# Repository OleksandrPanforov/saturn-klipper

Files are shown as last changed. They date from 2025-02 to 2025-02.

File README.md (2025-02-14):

# Elegoo Saturn 1 with Klipper

## Table of contents

1. [What and why?](#1-what-and-why)
2. [Bill of materials](#2-bill-of-materials)
3. [Hardware setup](#3-hardware-setup)
4. [Software setup](#4-software-setup)
5. [Addons](#5-addons)
6. [Troubleshooting](#6-troubleshooting)
7. [My experience](#7-my-experience)
8. [Next steps](#8-next-steps)

## 1. What and why?

### What?
**Elegoo Saturn 1 resin printer with Klipper onboard.**
<p align="center">
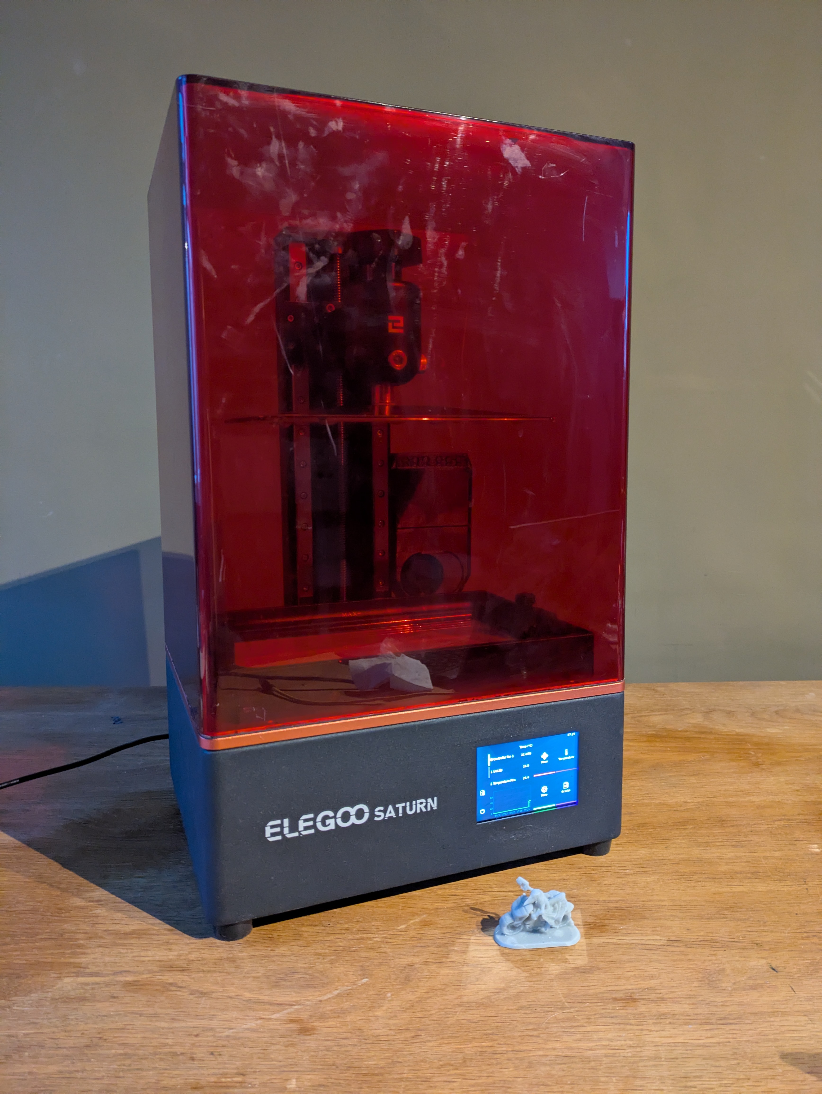
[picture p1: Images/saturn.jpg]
Saturn preview

</p>

Based on a donor printer, with or without a working screen, neatly packed in the stock enclosure. 
The older resin printers are dirt cheap and widely available, especially with a busted screen. That is, an easy and cost-effective starting point. 

### Why?
**I think, proprietary printers suck.** 

I've been working with resin printers for a while now, and the way any upgrade is either buying a new model, or perform complicated hacks is what I really disliked about the tech. Which is not the case with hobby-level FDM. 

Naturally, when I found out the [PR to get Klipper support for mSLA](https://github.com/Klipper3d/klipper/pull/6575) exists, I got an old Saturn and started tinkering. 

### Before you start
The Elegoo Saturn 1 was released in 2020 with a 8.9" 4k display onboard. By no means it is a modern printer with ultra-high resolution. That is, to set up the expectations, be aware this conversion might not suite your use case. Especially given the amount of tinkering required to make it work. As a cherry on top, just the electronics with a screen could easily cost the same as the new Elegoo Saturn 4. Not that I want to discourage you - this is an awesome project. Just be sure you understand what you are going to step into.

> ⚠️ And while we're on it, proceed at your own risk. I am not responsible for property damage, injuries, or any unwanted consequences occuring from following this manual. <br> <br>⚠️ It worked on my machine, that's the best I can tell. You have been warned.

## 2. Bill of materials

### Required
|Name|Qty|Note|
|-|-|-|
|[BTT Manta M4P](https://biqu.equipment/products/manta-m4p-m8p?variant=39847241056354)|1| |
|[Raspberry CM4](https://www.raspberrypi.com/products/compute-module-4/?variant=raspberry-pi-cm4001000)|1|**4Gb + Wifi + Lite recommended.** I was not able to use BTT CB1, due to troubles with configuring display with the proper overlay. |
|[CM4 cooling](https://www.waveshare.com/product/cm4-heatsink-b.htm) |1|Passive should work, active won't hurt for longer print jobs. |
|[TMC2209 stepper driver](https://biqu.equipment/products/bigtreetech-tmc2209-stepper-motor-driver-for-3d-printer-board-vs-tmc2208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) |1| |
|[PJ089Y2V5 8.9" mono screen](https://aliexpress.com/item/1005004398973695.html) |1|It is also possible to use TM089CFSP01 with the same config. |
|[HDMI driver for the display](https://aliexpress.com/item/1005004398973695.html) |1| |
|[BTT TFT35 SPI](https://biqu.equipment/products/bigtreetech-tft35-spi-v2-1-touchscreen-io2can-module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) |1|While not the best for the job, it fits best to the stock case. |
|HDMI cable |1|15-30cm, for connecting the HDMI driver |
|USB A to USB C cable |1|15-30cm, for connecting the HDMI driver. |
|KCD1 switch |1||
|5.5x2.5 power socket |1||
|[Printed parts]()|1||
|M3x40 screws|4||

### Reused from a donor printer
|Name|Qty|Note|
|-|-|-|
|NEMA17 stepper motor|1||
|Z axis kinematics|1||
|Z endstop|1|You will need to change the pinout of the connector.|
|Enclosure|1||
|Power supply unit|1||
|UV LED array with driver|1||
|Buildplate|1||
|Resin vat|1||
|Glass under the screen|1|Can be purchased with the screen, but reusing is slightly cheaper.|
|Enclosure fans|2||
|Most of the fasteners|1||

### Optional
|Name|Qty|Note|
|-|-|-|
|USB keystone |1||
|Temperature sensor|1| PT1000 is configured, it is a good option for monitoring the UV LED array temperature.|
|RJ45 keystone |1| |
|[SUNON 24V DC 0.65W 50x50x15mm](https://aliexpress.com/item/1005007898152811.html) |2|Stock fans can be reused.|
|[Nevermore Nano](https://www.printables.com/model/1176031-nevermore-v6-nano-single-fan-micro)|1|Any coal filter with fan will do. Strongly advised, resin fumes are a serious matter.|

## 3. Hardware setup
### Preparation
#### Screen
Important thing to consider when getting a Saturn is the screen model.
Originally, Saturns were shipped with either PJ089Y2V1 or TM089CFSP01.

> ❗ PJ089Y2V**5** has a different pinout from PJ089Y2V**1**, so HDMI driver will also be different.

#### Printed parts
ABS or ASA would be best to use. Little to no load expected on the printed parts, however there might be some relatively high temperatures around the UV LED array. 

#### Z-endstop
[EE-SX674](https://www.ia.omron.com/data_pdf/cat/ee-sx47_67_ds_e_13_4_csm483.pdf) with 3 pins connector should be wired as 

🟫Brown (5V)<br> 
🟦Blue (GND)<br>
⬛Black (Signal)

<p align="center">
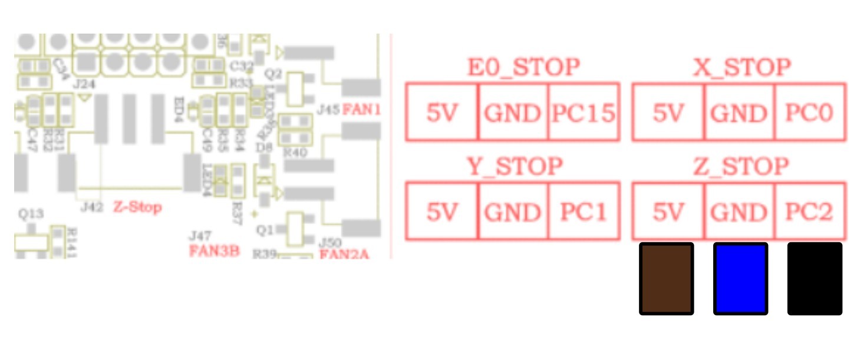
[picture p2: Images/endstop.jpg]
Z endstop wiring
    
</p>

### Disassembly 
From a donor printer, only enclosure, UV LED with driver and kinematics are needed. Screen only if it can be used with HDMI driver. 

### Assembly
0. Take the bottom part of the enclosure.
1. Install the BTT TFT35 using the printed mount. 
<p align="center">
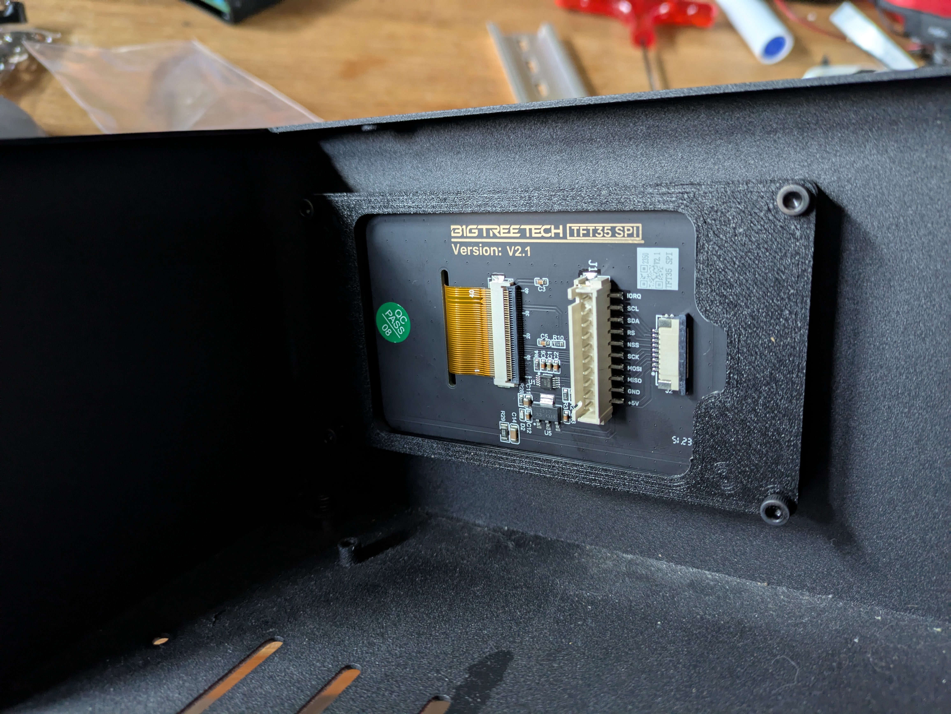
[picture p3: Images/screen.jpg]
BTT TFT35 mount
    
</p>

2. Insert the printed slot caps.
3. Install the mainboard using the printed mount.
4. Install the HDMI driver sing the printed mount.
5. Rotate and install the LED driver.

<p align="center">
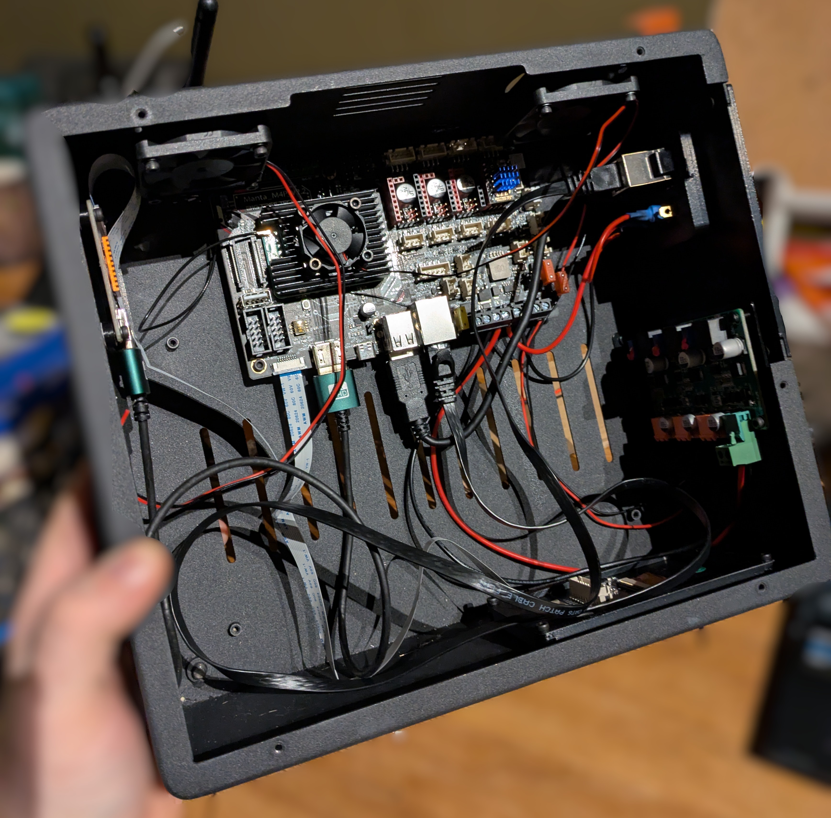
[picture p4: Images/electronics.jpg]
Electronics installed
    
</p>

6. Connect to the mainboard:
    + HDMI driver
    + LED driver
    + Power
    + BTT TFT35 SPI
    + Fans
    + Keystones, if used 

> ⚠️ This is the point where I suggest configuring the firmware, since after the UV LED is installed, the access to microsd card slot is tight, as well to the connectors.

7. Connect the UV LED array to the LED driver, then using the printed spacers and M3x40 screws install it in place.

<p align="center">
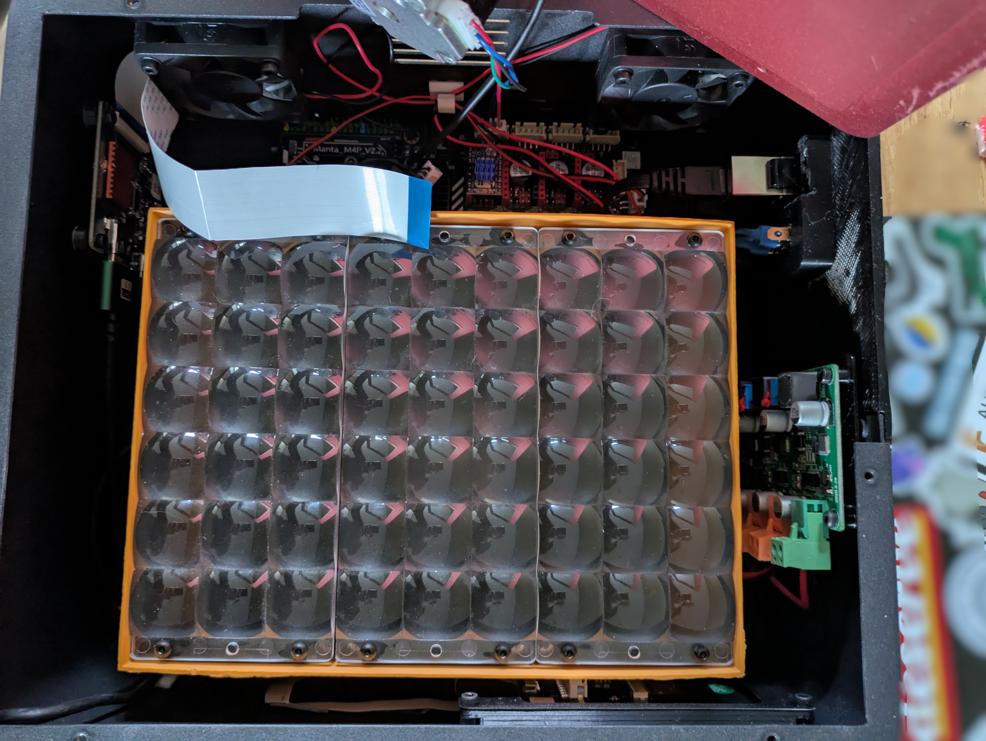
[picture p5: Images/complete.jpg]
UV LED array installed
    
</p>

> On this photo the stepper driver is in the wrong slot. It should be Z. Other than that, this is how everything should look at this point.
8. Connect to the mainboard:
    + Stepper motor
    + Z endstop
9. Connect the screen.
10. Screw the top part of the enclosure to the bottom. 
11. Calibrate as per [this guide](https://github.com/sn4k3/klipper-msla?tab=readme-ov-file#4-calibrate)
12. Make a test run as described in [this guide](https://github.com/sn4k3/klipper-msla?tab=readme-ov-file#5-final-run).

## 4. Software setup
### Firmware
Best starting point is [sn4k3/klipper-msla](https://github.com/sn4k3/klipper-msla). 
When following the manual, keep in mind the MCU is different, refer to [printer.cfg](/Software/printer.cfg). 

> ⚠️ In the configuration the safe z move is set to 180, however it's totally possible to go up to 200 safely. 

If you plan to use BTT TFT35, the setup process is [described here](https://github.com/stadie/btt_tft35spi_rpi). 

I highly encourage to set up [Samba](https://pimylifeup.com/raspberry-pi-samba/) to the printer folder of virtual_sdcard, i.e. ~/printer_data/gcodes.

### Slicer settings
Refer to [UVTools wiki](https://github.com/sn4k3/UVtools/wiki/Setup-PrusaSlicer)

Present [config.ini](/Software/config.ini) is mostly for reference.

### Slicing
1. Slice with [Prusaslicer](https://www.prusa3d.com/page/prusaslicer_424/) to .sl1 file.
2. Open with [UVTools](https://github.com/sn4k3/UVtools).
3. File -> Export to upload the folder to path mapped to Samba.

## 5. Addons
### Filter
As a big fan of [Nevermore3d](https://github.com/nevermore3d) filters I was quite sad Micro won't fit in the stock case. 

That's why I made remix for a half-width Micro. [Nano v6](https://www.printables.com/model/1176031-nevermore-v6-nano-single-fan-micro) is available on Printables. I simply drilled a hole in a vertical profile and screwed the filter with an M3 screw.

<p align="center">
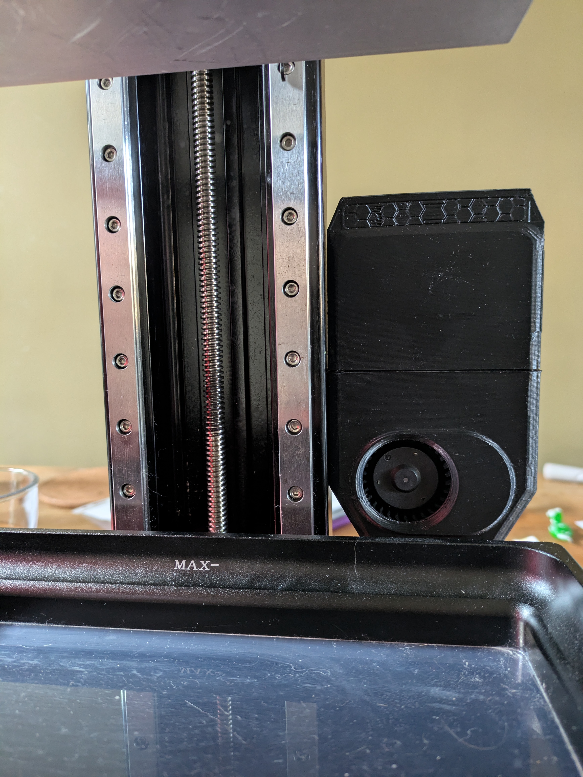
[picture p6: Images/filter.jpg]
Nevermore Nano
    
</p>

## 6. Troubleshooting
### Internal error on command:"M1451"
Likely, an image is missing. Check if all the images for the layers are present. 
## 7. My experience
It took me some time to pull the trigger on this project. I do like how it turned out, still there were ups and downs along the way. Namely,

🟥 I didn't like
+ Adapting the stock housing. Frankly, Elegoo Saturn 1 is not the most spacious printer out there. 
+ The total price of the printer, accounting for the new components. It was worth it, but it doesn't mean it was cheap. 

🟨 I'm still grasping
+ The new workflow. I used to work with Lychee Slicer for mSLA and Prusa Slicer for FDM, so I'm climbing the learning curve. It is mostly easy, the documentation of both Prusa Slicer and UVTools is amazingly detailed.
+ How long will it take for the LCD to die. My guess is, raising the UVLED array closer to the screen will not help with the lifespan. But how many hours are we talking about, exactly? 

🟩 I absolutely love
+ Klipper. 
+ [mSLA fork](https://github.com/sn4k3/klipper-msla). The setup is well-documented, easy to follow, and [sn4k3](https://github.com/sn4k3) is quick to respond in case of anything confusing. 
+ How easy it is to add stuff. Filter was a breeze to configure, I'm looking into a vat heater and it's much much easier to get the desired behavior than with a proprietary boards.
+ Troubleshooting and extensive logs. The days of guessing why the print was stopped for no apparent reason are gone. 
+ Flexibility of the repairs. Aside from the screen and UV array, I now can throw in whatever spare things I have from my FDM printers, without a need to wait for the manufacturer's support/AliExpress to send me specific parts.
+ Open Source electronics. Sure, there are always ways to reverse-engineer the fix, like with the infamous [backlight always on issue on Saturn](https://blog.honzamrazek.cz/2021/06/fixing-the-backlight-always-on-problem-on-elegoo-saturn/), but it saves time when I don't have to.

🟪 It would be nice to
+ Have more meaningful information on the KlipperScreen. Naturally, it is aimed to FDM, and for the most part it's also good for mSLA.

## 8.  Next steps
At some point I would love to design the same thing without the need of a donor printer. Pretty sure it's not a nearby future matter, but that is in my backlog.

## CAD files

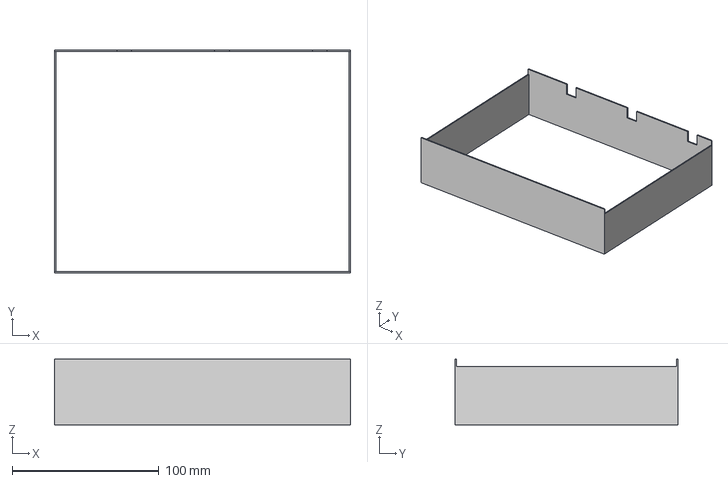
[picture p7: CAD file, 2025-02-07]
Hardware/To_Print/Step/LED_cover.step
202.0 x 152.0 x 45.0 mm

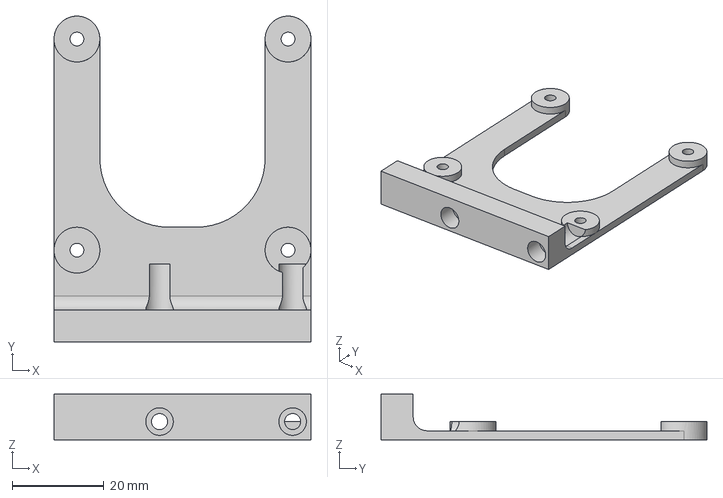
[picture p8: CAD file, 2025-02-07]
Hardware/To_Print/Step/Driver_mount.step
56.0 x 71.0 x 10.0 mm

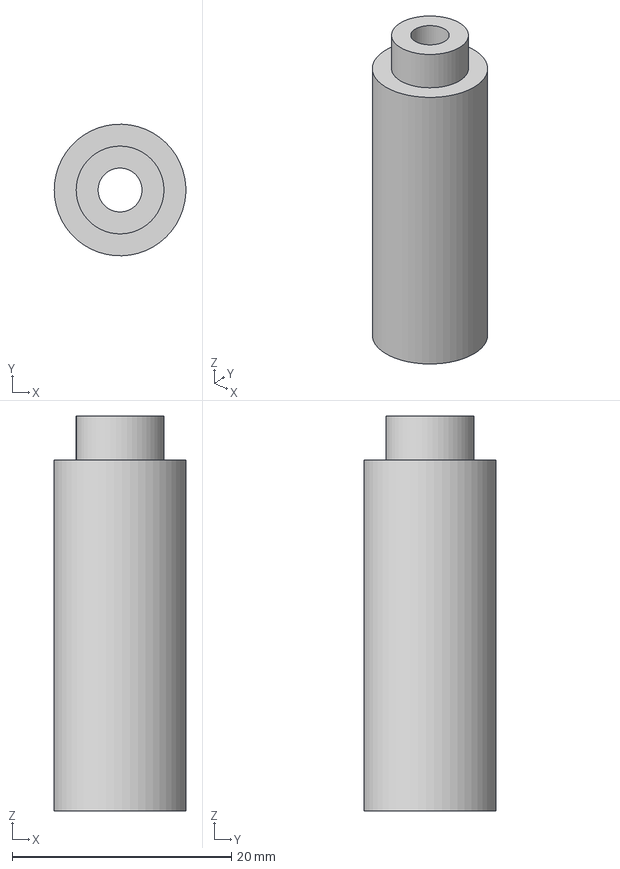
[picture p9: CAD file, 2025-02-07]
Hardware/To_Print/Step/LED_spacer.step
12.0 x 12.0 x 36.0 mm

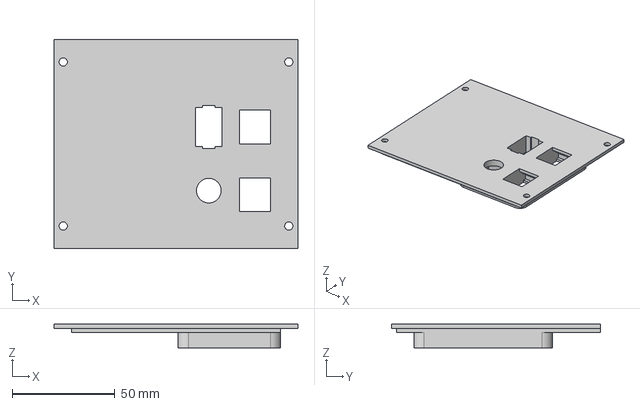
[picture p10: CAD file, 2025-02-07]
Hardware/To_Print/Step/Side_cover.step
119.0 x 102.0 x 11.5 mm

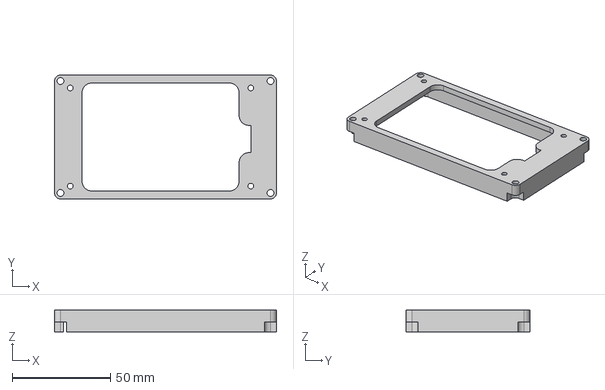
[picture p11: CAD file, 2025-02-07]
Hardware/To_Print/Step/BTT_TFT_35_SPI_adapter.step
113.1 x 63.1 x 11.0 mm

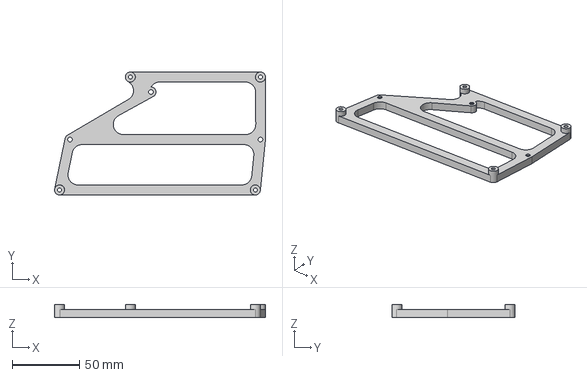
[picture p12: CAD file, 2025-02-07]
Hardware/To_Print/Step/Manta_M4P_mount.step
157.3 x 91.7 x 10.0 mm

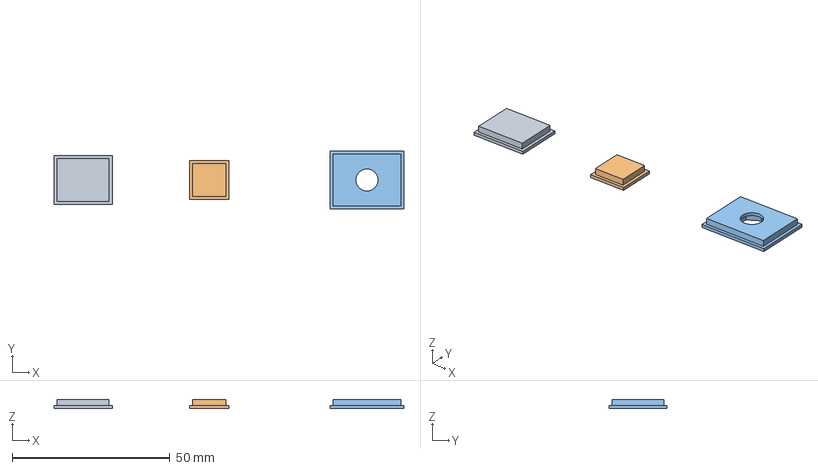
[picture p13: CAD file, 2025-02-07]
Hardware/To_Print/Step/Slot_caps.step
111.0 x 18.5 x 3.00 mm

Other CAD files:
Hardware/To_Print/Stl/BTT_TFT_35_SPI_adapter.stl
Hardware/To_Print/Stl/Driver_mount.stl
Hardware/To_Print/Stl/LED_cover.stl
Hardware/To_Print/Stl/LED_spacer.stl
Hardware/To_Print/Stl/Manta_M4P_mount.stl
Hardware/To_Print/Stl/Side_cover.stl
Hardware/To_Print/Stl/Slot_caps.stl

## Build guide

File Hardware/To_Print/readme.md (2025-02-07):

## Printed parts

|Name|Qty|Note|
|-|-|-|
|BTT_TFT_35_SPI_adapter|1||
|Driver_mount|1||
|LED_spacer|4||
|Manta_M4P_mount|1||
|Side_cover|1||
|Slot_caps|1|Set of 3. Only the one with an antenna mount is **required**.|
|LED_cover|1|**Optional**|

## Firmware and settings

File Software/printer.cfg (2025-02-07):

[mcu]
serial: /dev/serial/by-id/usb-Klipper_stm32g0b1xx_1F00350019504B5735313920-if00


[virtual_sdcard]
path: ~/printer_data/gcodes
on_error_gcode: CANCEL_PRINT

[pause_resume]

[display_status]

[respond]

# The sections below here are required for the macros to work. If your config
# already has some of these sections you should merge the duplicates into one
# (or if they are identical just remove one of them).
[idle_timeout]
gcode:
  _KM_IDLE_TIMEOUT # This line must be in your idle_timeout section.

[save_variables]
filename: ~/printer_data/variables.cfg # UPDATE THIS FOR YOUR PATH!!!

[stepper_z]
step_pin: PB0
dir_pin: !PC5
enable_pin: !PB1
microsteps: 16
rotation_distance: 2
endstop_pin: ^!PC2
position_endstop: 0
position_max: 170

[tmc2209 stepper_z]
uart_pin: PC9
run_current: 0.900
hold_current: 0.800
diag_pin: 

[output_pin msla_uvled]
pin: PD8
pwm: True
cycle_time: 0.01 # 100Hz

[msla_display]
model: PJ089Y2V5
pixel_format: Mono
framebuffer_index: 0
resolution_x: 3840
resolution_y: 2400
pixel_width: 0.05
pixel_height: 0.05
cache: 1
uvled_output_pin_name: msla_uvled

[temperature_sensor temperature_mcu]
sensor_type: temperature_host
#min_temp: 0
max_temp: 90


[pwm_cycle_time beeper] 
pin: EXP1_1

[display] 
lcd_type: uc1701 
cs_pin: EXP1_3 
a0_pin: EXP1_4 
rst_pin: EXP1_5 
contrast: 63 
encoder_pins: ^EXP2_5, ^EXP2_3 
click_pin: ^!EXP1_2 

[printer]
manufacturing_process: mSLA
kinematics: zaxis
max_velocity: 10
max_accel: 25
max_z_velocity: 10
max_z_accel: 25

[board_pins]
aliases:
    # EXP1 header
    EXP1_1=PD6,  EXP1_3=PB9,  EXP1_5=PA15, EXP1_7=PA9,   EXP1_9=<GND>,
    EXP1_2=PB8,  EXP1_4=PC3,  EXP1_6=PA10, EXP1_8=PB5,   EXP1_10=<5V>,
    # EXP2 header
    EXP2_1=PB14, EXP2_3=PC11, EXP2_5=PC12, EXP2_7=PC13,  EXP2_9=<GND>,
    EXP2_2=PB13, EXP2_4=PA8,  EXP2_6=PB15, EXP2_8=<RST>, EXP2_10=<NC>

[gcode_macro _km_options]
variable_tmc_safe_home_current: 0.23
variable_menu_show_octoprint: False
# Z position to park toolhead (set "max" to infer from stepper config).
variable_park_z: 50.0
variable_m600_park_z: "max"
variable_print_end_park_z: "max"
variable_print_start_fan_power: 200
gcode:
  SET_VELOCITY_LIMIT ACCEL=5
gcode:
  GCODE_ON_PRINT_STATUS STATUS=printing COMMAND="CUSTOM_START" ARGS=1 WHEN=ALWAYS TYPE=ENTER
  GCODE_ON_PRINT_STATUS STATUS=completing COMMAND="CUSTOM_END" ARGS=1 WHEN=ALWAYS TYPE=ENTER


[fan_generic nevermore]
pin: PD2

[temperature_sensor UVLED]
sensor_type: PT1000
pullup_resistor: 4700
sensor_pin: PA0
#min_temp: 0
max_temp: 96

[temperature_fan controller_fan_1]
pin: PD3
max_power: 1
control: watermark
max_delta: 2
sensor_type: temperature_mcu
min_temp: 10
max_temp: 80
target_temp: 50

[fan]
pin: PD4
off_below: 0.25
max_power: 1.0
kick_start_time: 2
cycle_time: 0.0001 # 10KHz

[gcode_macro CUSTOM_START]
gcode:
  SET_FAN_SPEED FAN=nevermore SPEED=1.0

[gcode_macro CUSTOM_END]
gcode:
  SET_FAN_SPEED FAN=nevermore SPEED=0.0

# UART TMC2208 and TMC2209 safe home
[include klipper-msla-macros/*.cfg]
[include klipper-msla-macros/optional/tmc_safe_home.cfg]

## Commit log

2025-02-07 Initial commit
    Added files to print, images, printer config
    [BTT_TFT_35_SPI_adapter.step, BTT_TFT_35_SPI_adapter.stl, Driver_mount.step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]
2025-02-07 Folder structure, BOM
    [BTT_TFT_35_SPI_adapter.step, BTT_TFT_35_SPI_adapter.stl, Driver_mount.step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]
2025-02-07 Fixed wrong wiring for endstop
2025-02-07 Updated the slicing flow
